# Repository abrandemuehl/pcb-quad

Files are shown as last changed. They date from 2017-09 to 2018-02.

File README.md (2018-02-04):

# UIUC ECE395 PCB Quadcopter Project
The goal of the project was to design a quadcopter with a PCB frame and as many
parts as possible soldered directly onto it. We put an STM32F4, and a BNO055 
IMU onto the board, and purchased external ESC's for the motors.

### Results
Due to difficulties with a parts order through the school, we were not able to 
sufficiently test the hardware before a final version was due. We missed a pull
up resistor on the BNO055's NRESET pin, causing it to constantly be in a state 
of reset, and making it unusable. We fixed it by taping our breakout board IMU 
onto the board, and connecting the necessary wires. After that, we had working 
hardware, but were not able to finish tuning the quadcopter before a failure 
broke one of the motors. We did not have a tuning rig, so we were forced to tune
it by attempting to hover at about floor level. Eventually, one of the motors 
that we used failed, ending the project with working hardware and software, but
incomplete tuning.

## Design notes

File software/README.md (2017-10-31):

# Single Board Quadcopter Software

Uses ST's [CMSIS distribution for the STM32F427xx](http://www.st.com/en/embedded-software/stsw-stm32065.html) for the chip specific information

## Setting up the linux serial port
`stty -F /dev/ttyUSB0 115200 cs8 -cstopb -parenb`

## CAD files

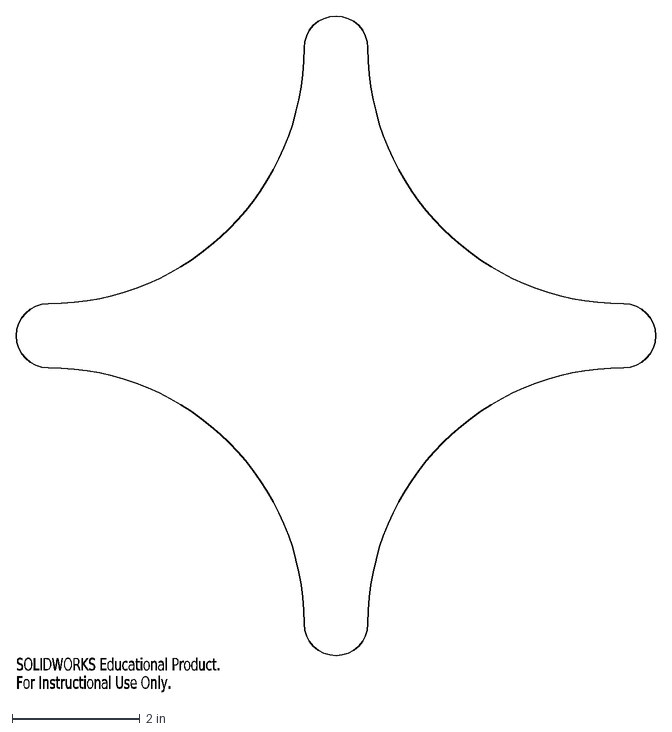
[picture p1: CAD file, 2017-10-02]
hardware/Board_Outline.DXF
SOLIDWORKS Educational Product.
For Instructional Use Only.

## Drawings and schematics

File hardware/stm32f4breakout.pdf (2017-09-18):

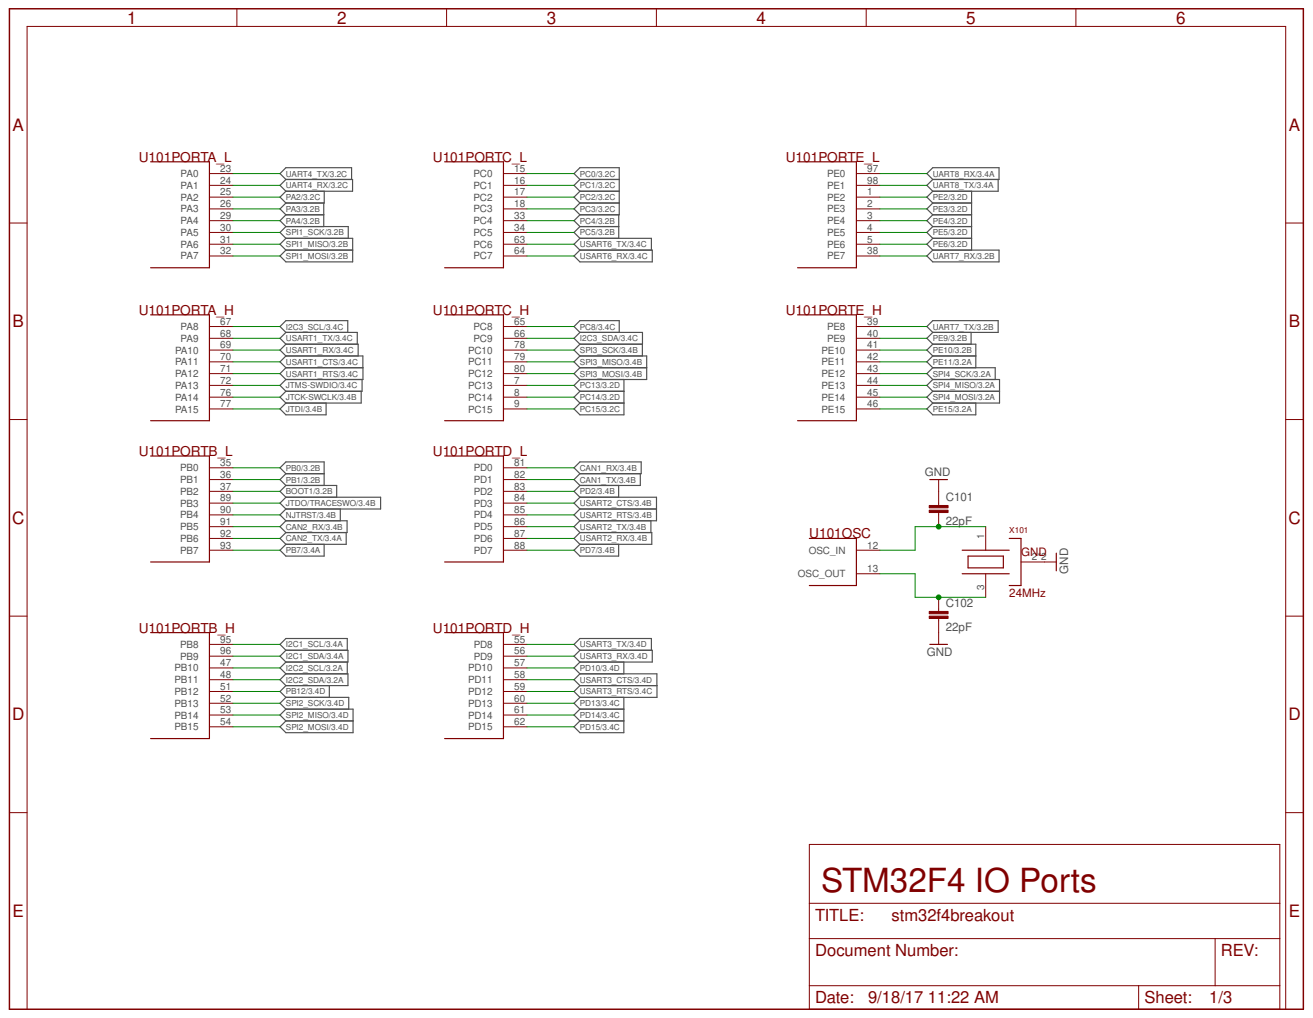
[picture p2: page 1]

Document Number: | REV:

Date: 9/18/17 11:22 AM | Sheet: 1/3

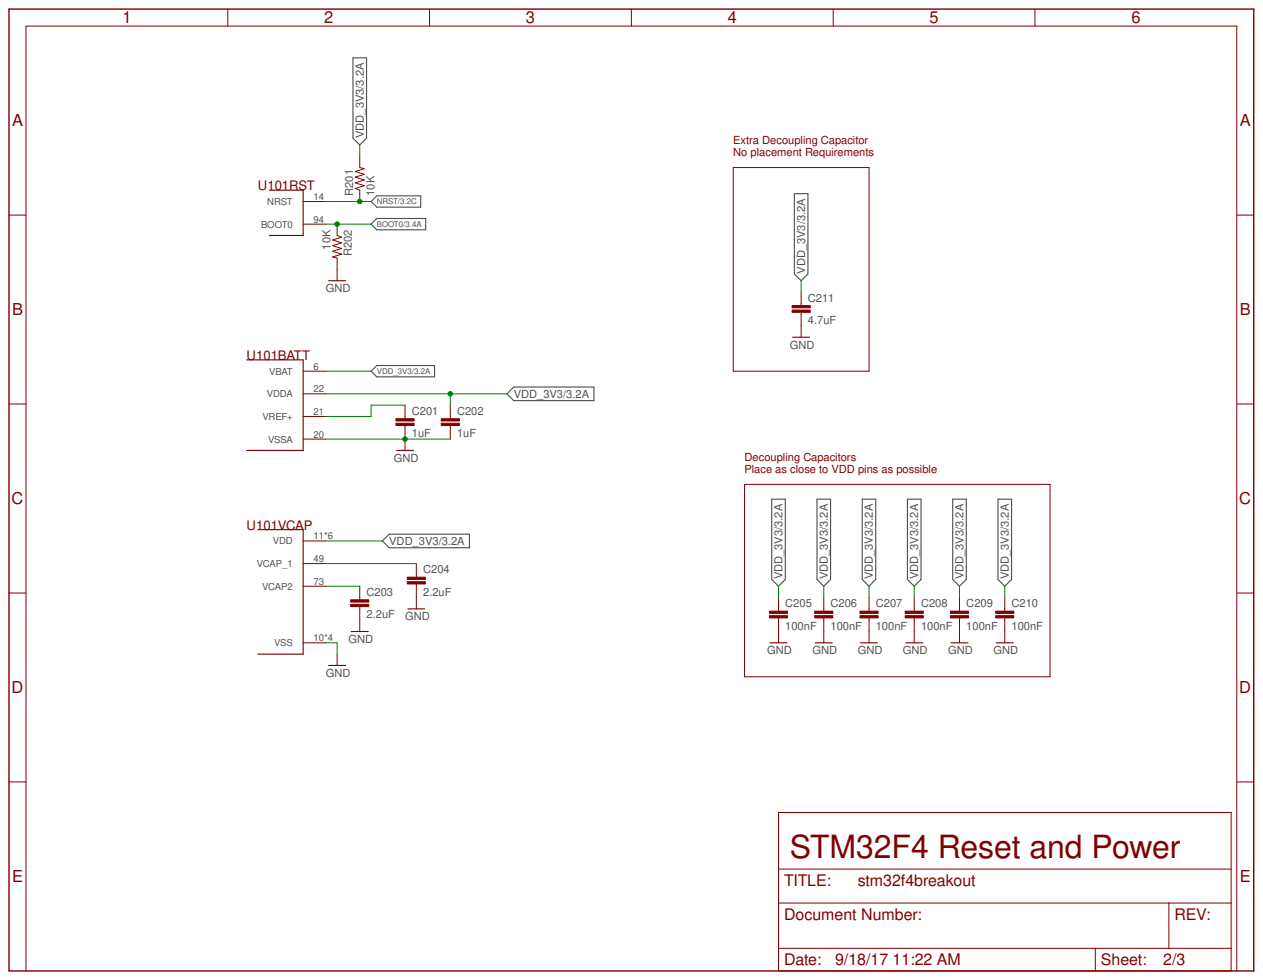
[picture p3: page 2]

Extra Decoupling Capacitor No placement Requirements A

Decoupling Capacitors Place as close to VDD pins as possible

Document Number: | REV:

Date: 9/18/17 11:22 AM | Sheet: 2/3

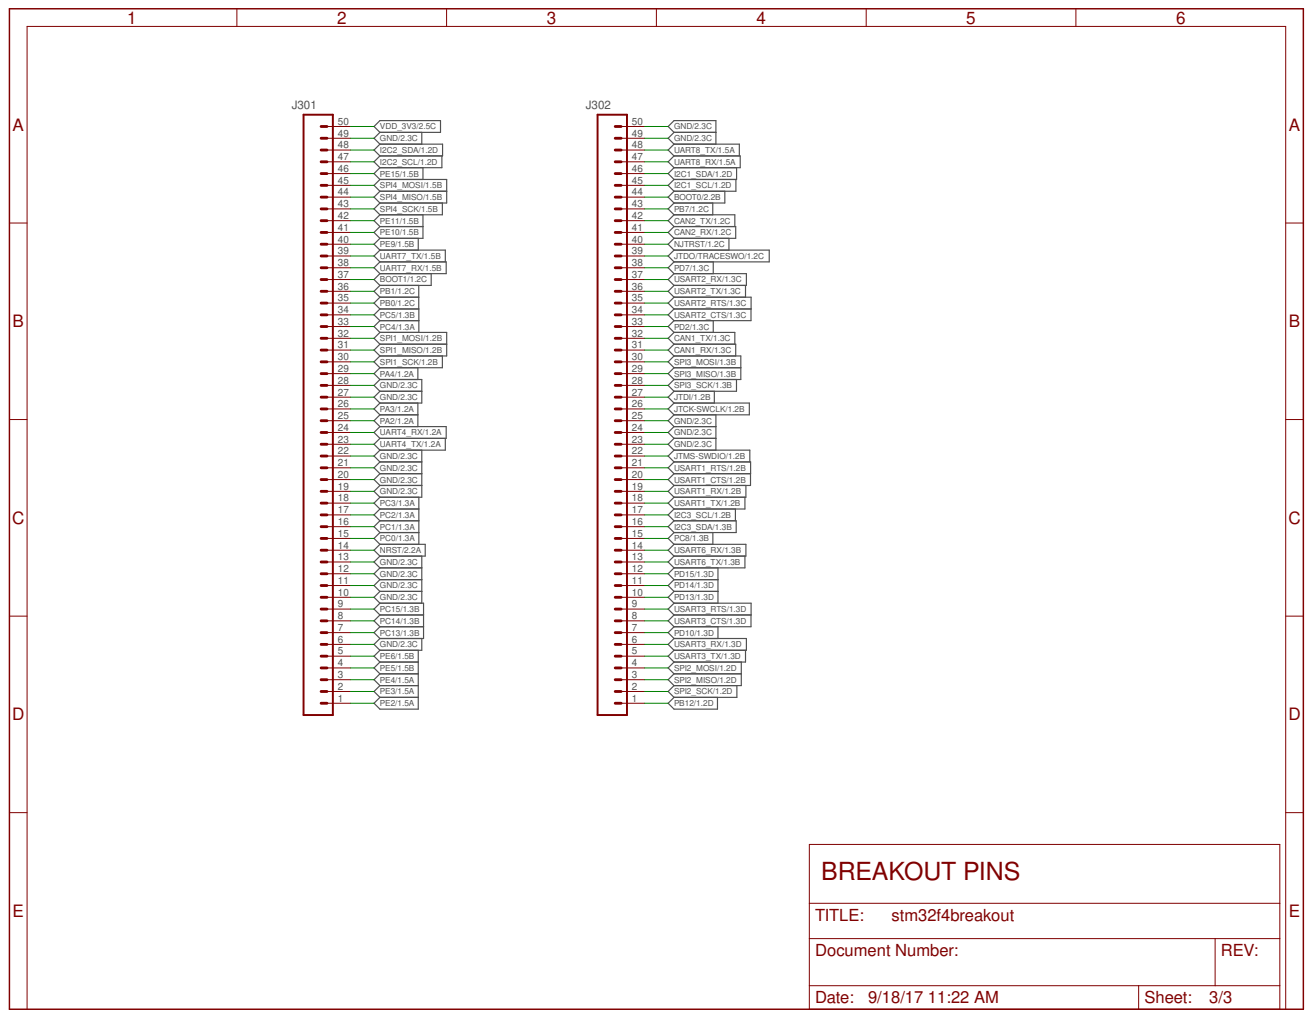
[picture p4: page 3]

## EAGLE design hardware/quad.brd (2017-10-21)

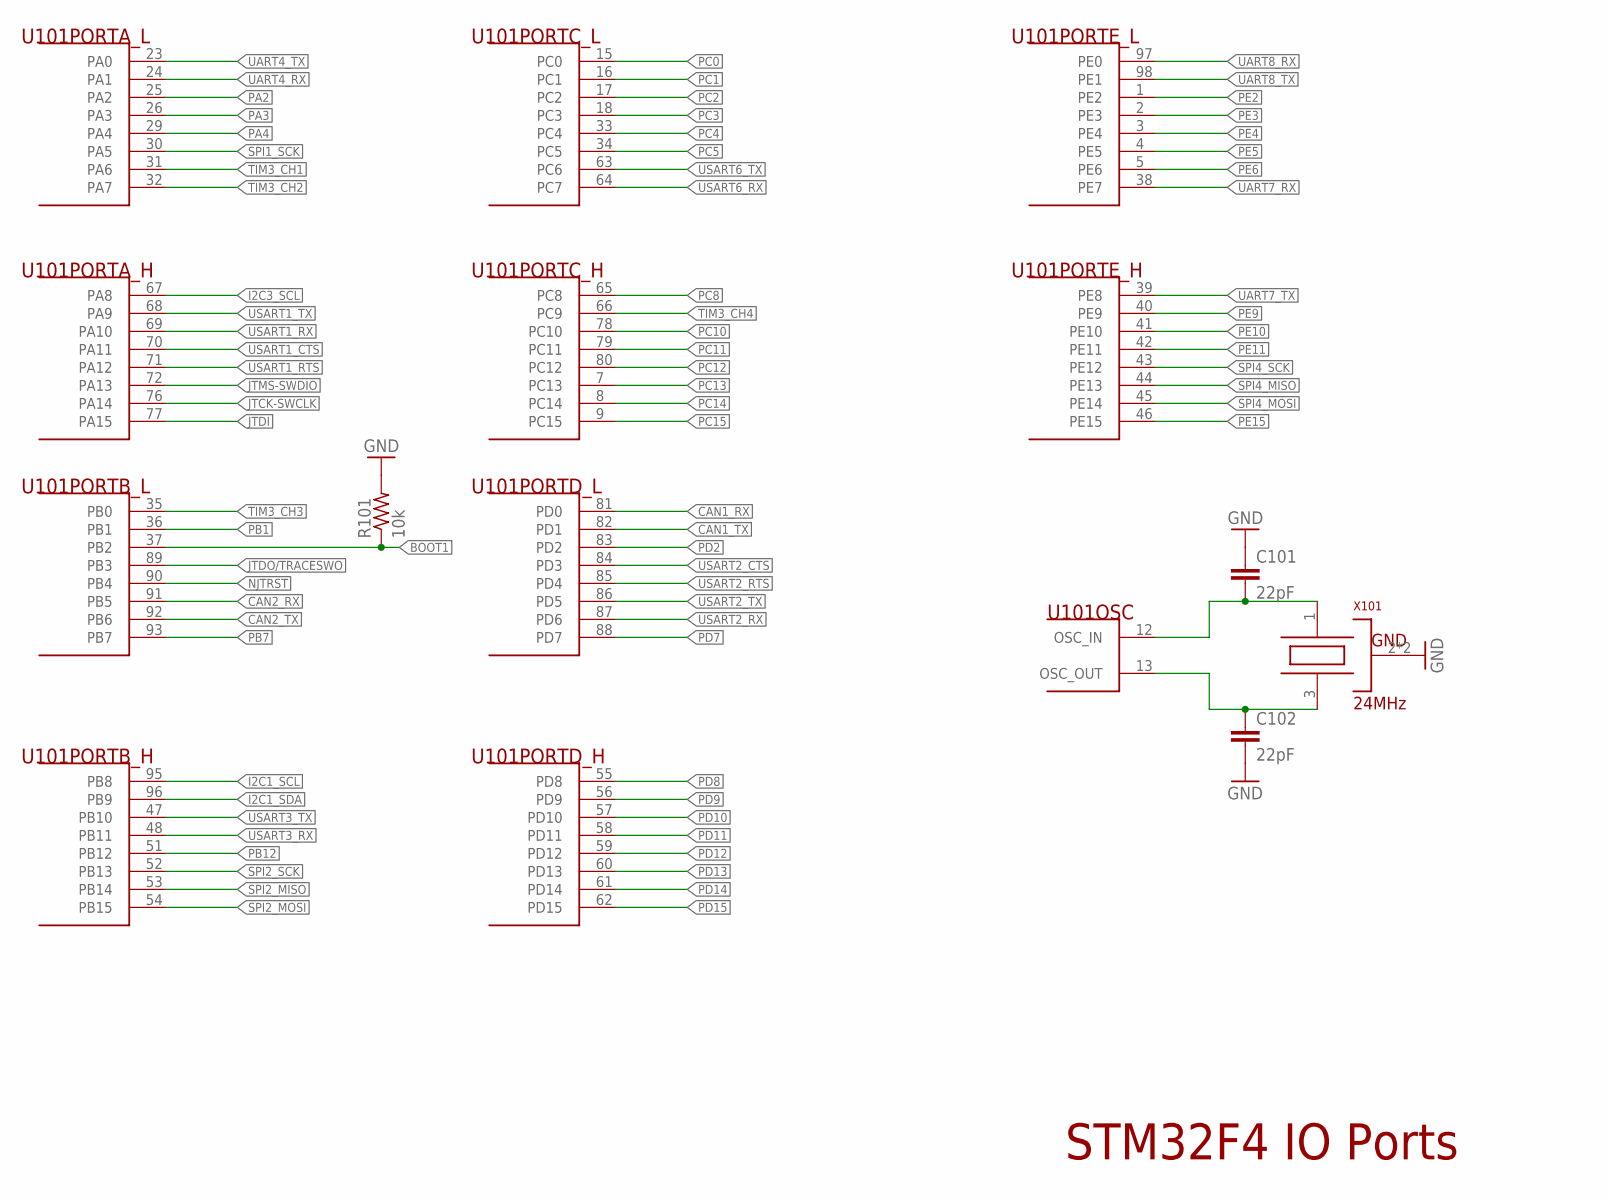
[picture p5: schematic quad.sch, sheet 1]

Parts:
C101, C102: 22pF; C0603
R101: 10k; R0603
U101: STM32F427VGT6; LQFP-100
X101: 24MHz; OSC3.2X2.5

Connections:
BOOT1: R101.1, U101.37 (PB2)
CAN1_RX: U101.81 (PD0)
CAN1_TX: U101.82 (PD1)
CAN2_RX: U101.91 (PB5)
CAN2_TX: U101.92 (PB6)
GND: C101.1, C102.2, R101.2, X101.2 (GND), X101.4 (GND); also elsewhere on the board
I2C1_SCL: U101.95 (PB8); also elsewhere on the board
I2C1_SDA: U101.96 (PB9); also elsewhere on the board
I2C3_SCL: U101.67 (PA8)
JTCK-SWCLK: U101.76 (PA14)
JTDI: U101.77 (PA15)
JTDO/TRACESWO: U101.89 (PB3)
JTMS-SWDIO: U101.72 (PA13)
NJTRST: U101.90 (PB4)
OSC_IN: C101.2, U101.12 (OSC_IN), X101.1 (OSC1)
OSC_OUT: C102.1, U101.13 (OSC_OUT), X101.3 (OSC2)
PA2: U101.25 (PA2)
PA3: U101.26 (PA3)
PA4: U101.29 (PA4)
PB1: U101.36 (PB1)
PB7: U101.93 (PB7)
PB12: U101.51 (PB12)
PC0: U101.15 (PC0)
PC1: U101.16 (PC1)
PC2: U101.17 (PC2)
PC3: U101.18 (PC3)
PC4: U101.33 (PC4)
PC5: U101.34 (PC5)
PC8: U101.65 (PC8)
PC10: U101.78 (PC10)
PC11: U101.79 (PC11)
PC12: U101.80 (PC12)
PC13: U101.7 (PC13)
PC14: U101.8 (PC14)
PC15: U101.9 (PC15)
PD2: U101.83 (PD2); also elsewhere on the board
PD7: U101.88 (PD7)
PD8: U101.55 (PD8)
PD9: U101.56 (PD9)
PD10: U101.57 (PD10)
PD11: U101.58 (PD11)
PD12: U101.59 (PD12)
PD13: U101.60 (PD13)
PD14: U101.61 (PD14)
PD15: U101.62 (PD15)
PE2: U101.1 (PE2)
PE3: U101.2 (PE3)
PE4: U101.3 (PE4)
PE5: U101.4 (PE5)
PE6: U101.5 (PE6)
PE9: U101.40 (PE9)
PE10: U101.41 (PE10)
PE11: U101.42 (PE11)
PE15: U101.46 (PE15)
SPI1_SCK: U101.30 (PA5)
SPI2_MISO: U101.53 (PB14)
SPI2_MOSI: U101.54 (PB15)
SPI2_SCK: U101.52 (PB13)
SPI4_MISO: U101.44 (PE13)
SPI4_MOSI: U101.45 (PE14)
SPI4_SCK: U101.43 (PE12)
TIM3_CH1: U101.31 (PA6); also elsewhere on the board
TIM3_CH2: U101.32 (PA7); also elsewhere on the board
TIM3_CH3: U101.35 (PB0); also elsewhere on the board
TIM3_CH4: U101.66 (PC9); also elsewhere on the board
UART4_RX: U101.24 (PA1)
UART4_TX: U101.23 (PA0)
UART7_RX: U101.38 (PE7)
UART7_TX: U101.39 (PE8)
UART8_RX: U101.97 (PE0)
UART8_TX: U101.98 (PE1)
USART1_CTS: U101.70 (PA11)
USART1_RTS: U101.71 (PA12)
USART1_RX: U101.69 (PA10); also elsewhere on the board
USART1_TX: U101.68 (PA9); also elsewhere on the board
USART2_CTS: U101.84 (PD3)
USART2_RTS: U101.85 (PD4)
USART2_RX: U101.87 (PD6)
USART2_TX: U101.86 (PD5)
USART3_RX: U101.48 (PB11); also elsewhere on the board
USART3_TX: U101.47 (PB10); also elsewhere on the board
USART6_RX: U101.64 (PC7)
USART6_TX: U101.63 (PC6)

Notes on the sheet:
STM32F4 IO Ports

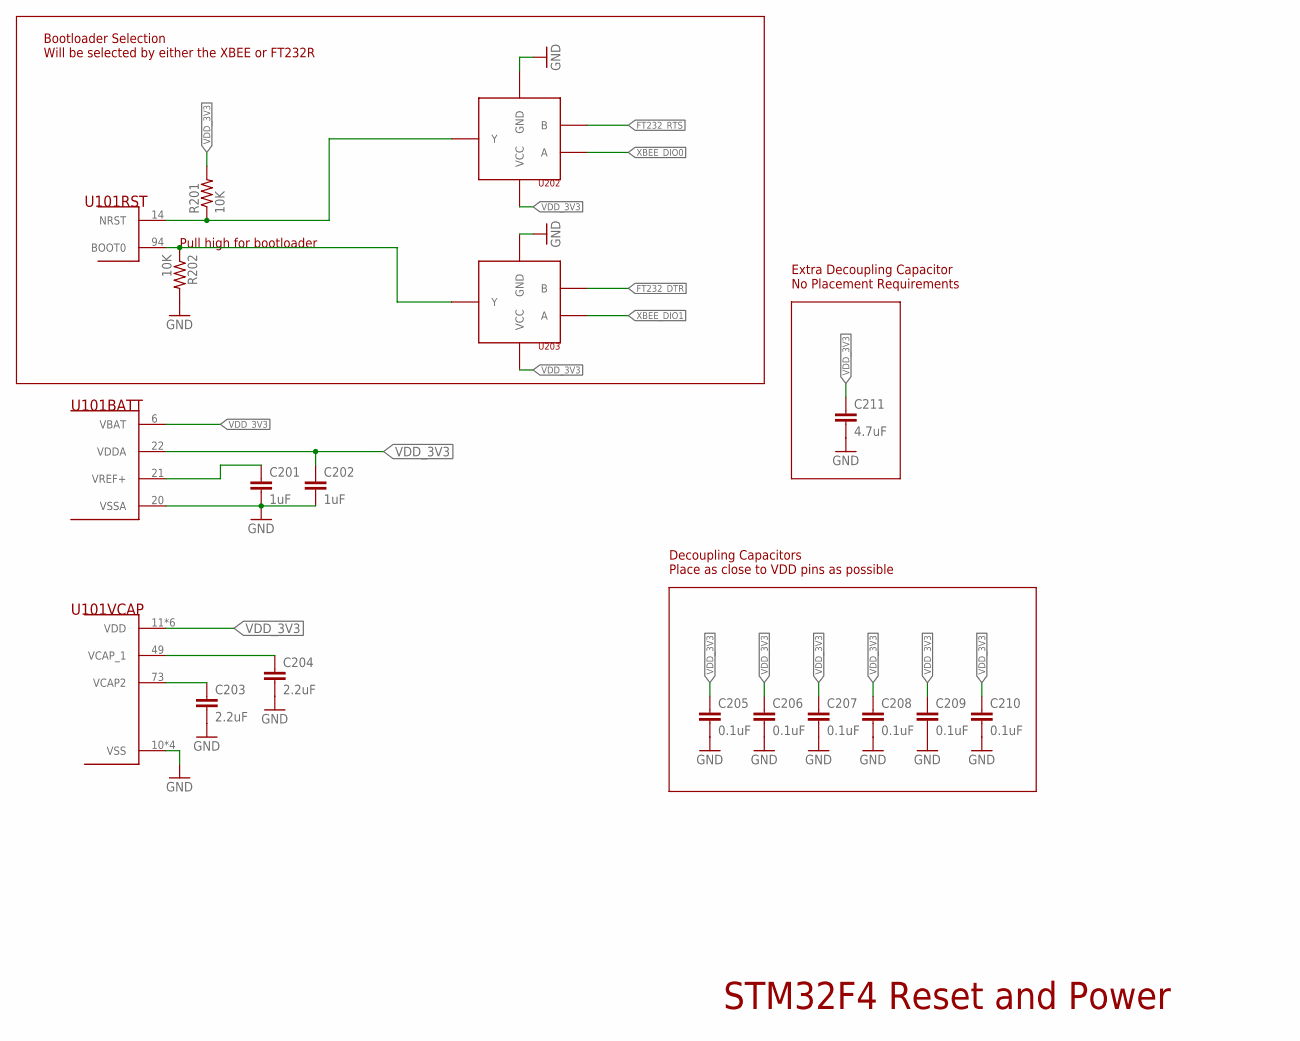
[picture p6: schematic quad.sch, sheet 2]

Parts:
C201, C202: 1uF; C0603
C203, C204: 2.2uF; C0603
C205, C206, C207, C208, C209, C210: 0.1uF; C0603
C211: 4.7uF; C0603
R201, R202: 10K; R0603
U101: STM32F427VGT6; LQFP-100
U202: AND_GATE; SOT23-5L
U203: SN74AHC1G32DBVR; SOT23-5L

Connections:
BOOT0: R202.1, U101.94 (BOOT0), U203.4 (Y)
FT232_DTR: U203.2 (B); also elsewhere on the board
FT232_RTS: U202.2 (B); also elsewhere on the board
GND: C201.2, C202.2, C203.2, C204.2, C205.2, C206.2, C207.2, C208.2, C209.2, C210.2, C211.2, R202.2, U101.10 (VSS), U101.20 (VSSA), U101.27 (VSS), U101.74 (VSS), U101.99 (VSS), U202.3 (GND), U203.3 (GND); also elsewhere on the board
NRST: R201.1, U101.14 (NRST), U202.4 (Y)
VCAP2: C203.1, U101.73 (VCAP2)
VCAP_1: C204.1, U101.49 (VCAP_1)
VDD_3V3: C201.1, C202.1, C205.1, C206.1, C207.1, C208.1, C209.1, C210.1, C211.1, R201.2, U101.6 (VBAT), U101.11 (VDD), U101.19 (VDD), U101.21 (VREF+), U101.22 (VDDA), U101.28 (VDD), U101.50 (VDD), U101.75 (VDD), U101.100 (VDD), U202.5 (VCC), U203.5 (VCC); also elsewhere on the board
XBEE_DIO0: U202.1 (A); also elsewhere on the board
XBEE_DIO1: U203.1 (A); also elsewhere on the board

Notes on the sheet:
STM32F4 Reset and Power
Decoupling Capacitors Place as close to VDD pins as possible
Extra Decoupling Capacitor No Placement Requirements
Pull high for bootloader
Bootloader Selection Will be selected by either the XBEE or FT232R

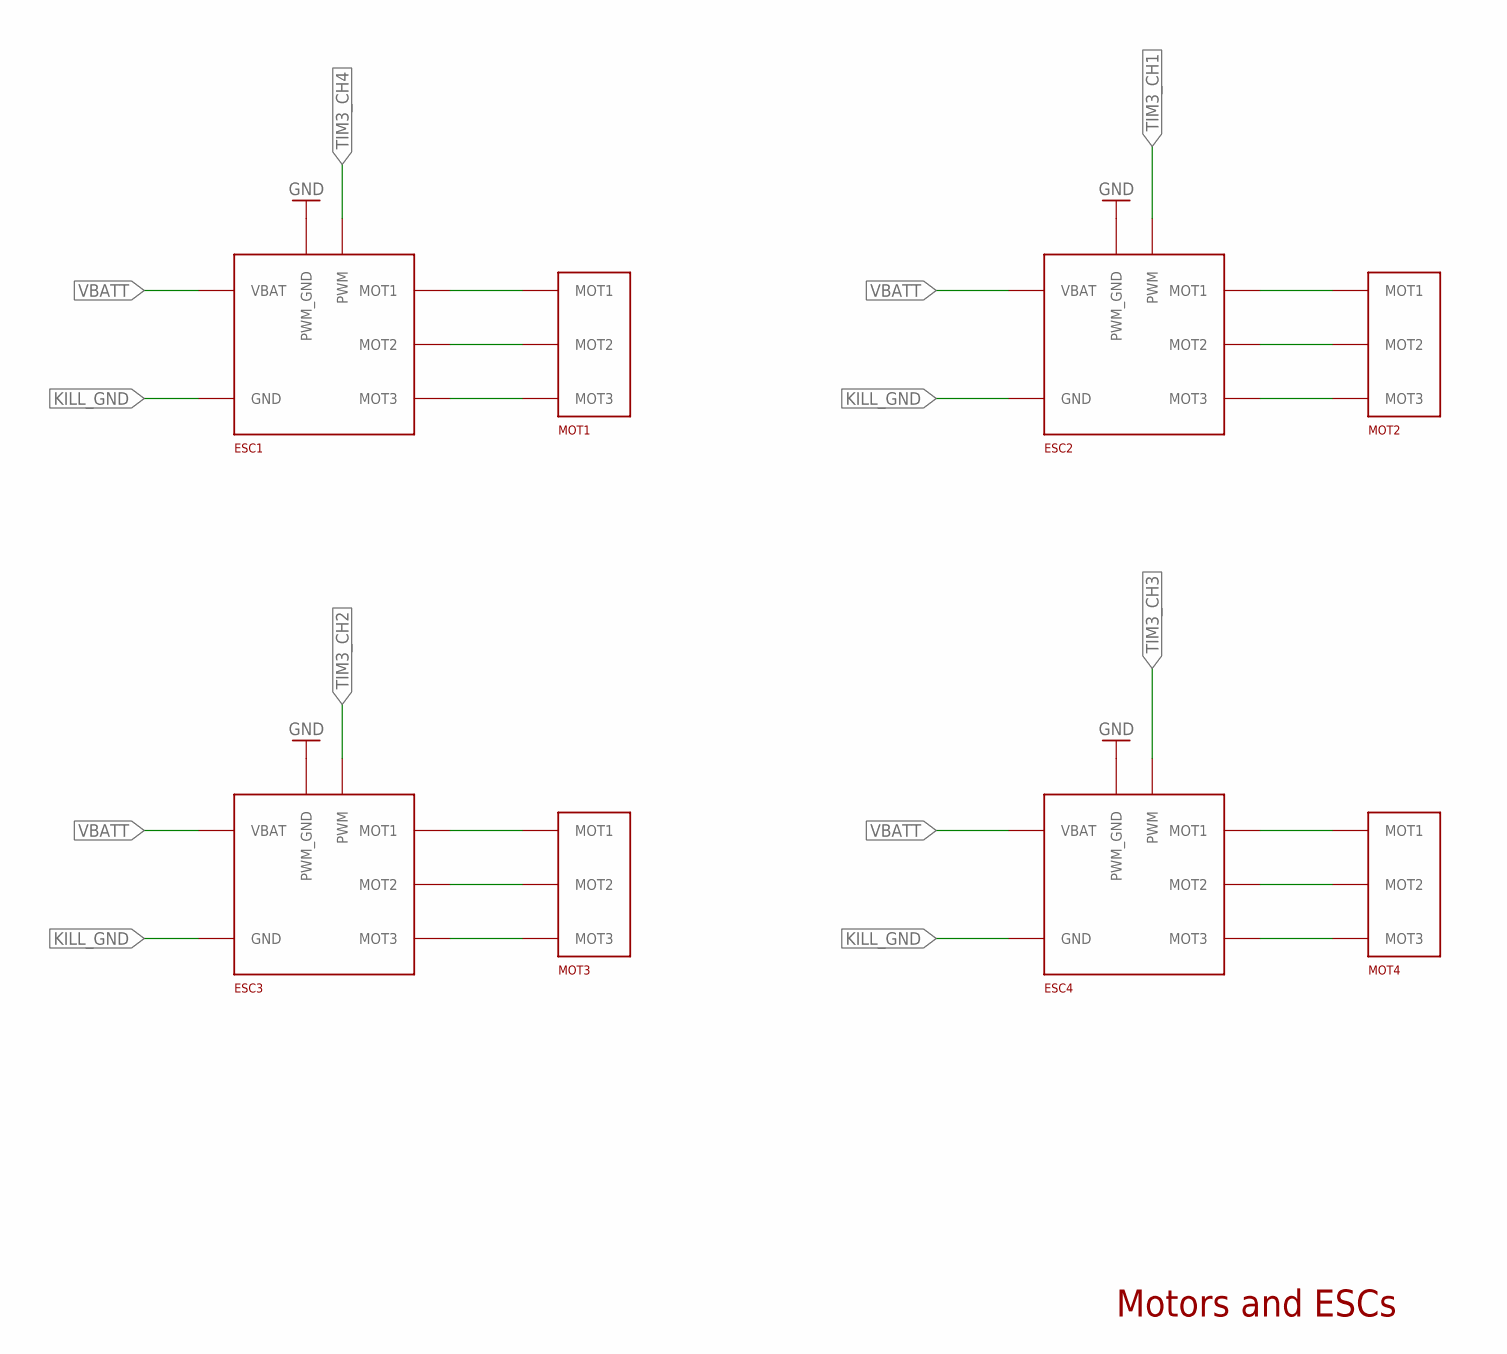
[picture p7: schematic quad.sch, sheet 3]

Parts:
ESC1, ESC2, ESC3, ESC4: AFRO_ESC
MOT1, MOT2, MOT3, MOT4: MOTOR

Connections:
GND: ESC1.PWM_GND, ESC2.PWM_GND, ESC3.PWM_GND, ESC4.PWM_GND; also elsewhere on the board
KILL_GND: ESC1.GND, ESC2.GND, ESC3.GND, ESC4.GND; also elsewhere on the board
MOT1_1: ESC1.MOT1, MOT1.MOT1
MOT1_2: ESC1.MOT2, MOT1.MOT2
MOT1_3: ESC1.MOT3, MOT1.MOT3
MOT2_1: ESC2.MOT1, MOT2.MOT1
MOT_2_2: ESC2.MOT2, MOT2.MOT2
MOT_2_3: ESC2.MOT3, MOT2.MOT3
MOT_3_1: ESC3.MOT1, MOT3.MOT1
MOT_3_2: ESC3.MOT2, MOT3.MOT2
MOT_3_3: ESC3.MOT3, MOT3.MOT3
MOT_4_1: ESC4.MOT1, MOT4.MOT1
MOT_4_2: ESC4.MOT2, MOT4.MOT2
MOT_4_3: ESC4.MOT3, MOT4.MOT3
TIM3_CH1: ESC2.PWM; also elsewhere on the board
TIM3_CH2: ESC3.PWM; also elsewhere on the board
TIM3_CH3: ESC4.PWM; also elsewhere on the board
TIM3_CH4: ESC1.PWM; also elsewhere on the board
VBATT: ESC1.VBATT (VBAT), ESC2.VBATT (VBAT), ESC3.VBATT (VBAT), ESC4.VBATT (VBAT); also elsewhere on the board

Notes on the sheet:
Motors and ESCs

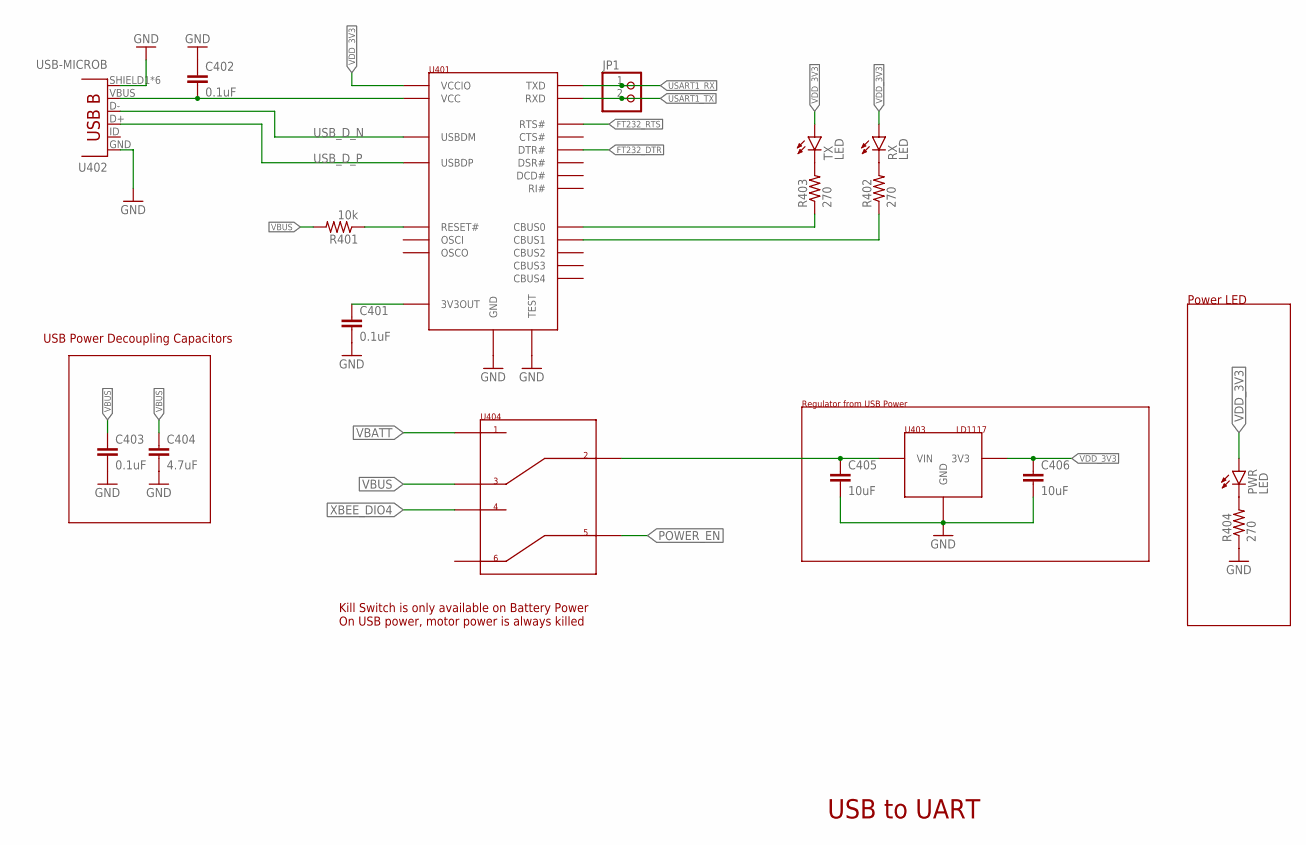
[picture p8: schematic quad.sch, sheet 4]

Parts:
C401, C402, C403: 0.1uF; C0603
C404: 4.7uF; C0603
C405, C406: 10uF; C0603
JP1: PINHD-1X2; 1X02
PWR: LED; LED-0603
R401: 10k; R0603
R402, R403, R404: 270; R0603
RX: LED; LED-0603
TX: LED; LED-0603
U401: FT232R; SSOP28
U402: USB-MICROB; USB-B-MICRO-SMD
U403: LD1117; SOT223
U404: MFS201N-16-Z

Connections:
FT232_DTR: U401.2 (DTR#); also elsewhere on the board
FT232_RTS: U401.3 (RTS#); also elsewhere on the board
GND: C401.2, C402.1, C403.2, C404.2, C405.2, C406.2, R404.1, U401.7 (GND), U401.18 (GND), U401.21 (GND), U401.25 (GND), U401.26 (TEST), U402.GND, U402.SHIELD1 (SHIELD), U402.SHIELD2 (SHIELD), U402.SHIELD3 (SHIELD), U402.SHIELD4 (SHIELD), U402.SHIELD5 (SHIELD), U402.SHIELD6 (SHIELD), U403.1 (GND); also elsewhere on the board
unnamed: R401.1, U401.19 (RESET#)
unnamed: C401.1, U401.17 (3V3OUT)
unnamed: R403.1, U401.23 (CBUS0)
unnamed: R402.1, U401.22 (CBUS1)
unnamed: R402.2, RX.C
unnamed: R403.2, TX.C
unnamed: PWR.C, R404.2
POWER_EN: U404.5; also elsewhere on the board
PWR: C405.1, U403.3 (VIN), U404.2
USART1_RX: JP1.1, U401.1 (TXD); also elsewhere on the board
USART1_TX: JP1.2, U401.5 (RXD); also elsewhere on the board
USB_D_N: U401.16 (USBDM), U402.D-
USB_D_P: U401.15 (USBDP), U402.D+
VBATT: U404.1; also elsewhere on the board
VBUS: C402.2, C403.1, C404.1, R401.2, U401.20 (VCC), U402.VBUS, U404.3
VDD_3V3: C406.1, PWR.A, RX.A, TX.A, U401.4 (VCCIO), U403.2 (3V3), U403.4 (3V3); also elsewhere on the board
XBEE_DIO4: U404.4; also elsewhere on the board

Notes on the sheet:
USB to UART
USB Power Decoupling Capacitors
Regulator from USB Power
Kill Switch is only available on Battery Power On USB power, motor power is always killed
Power LED

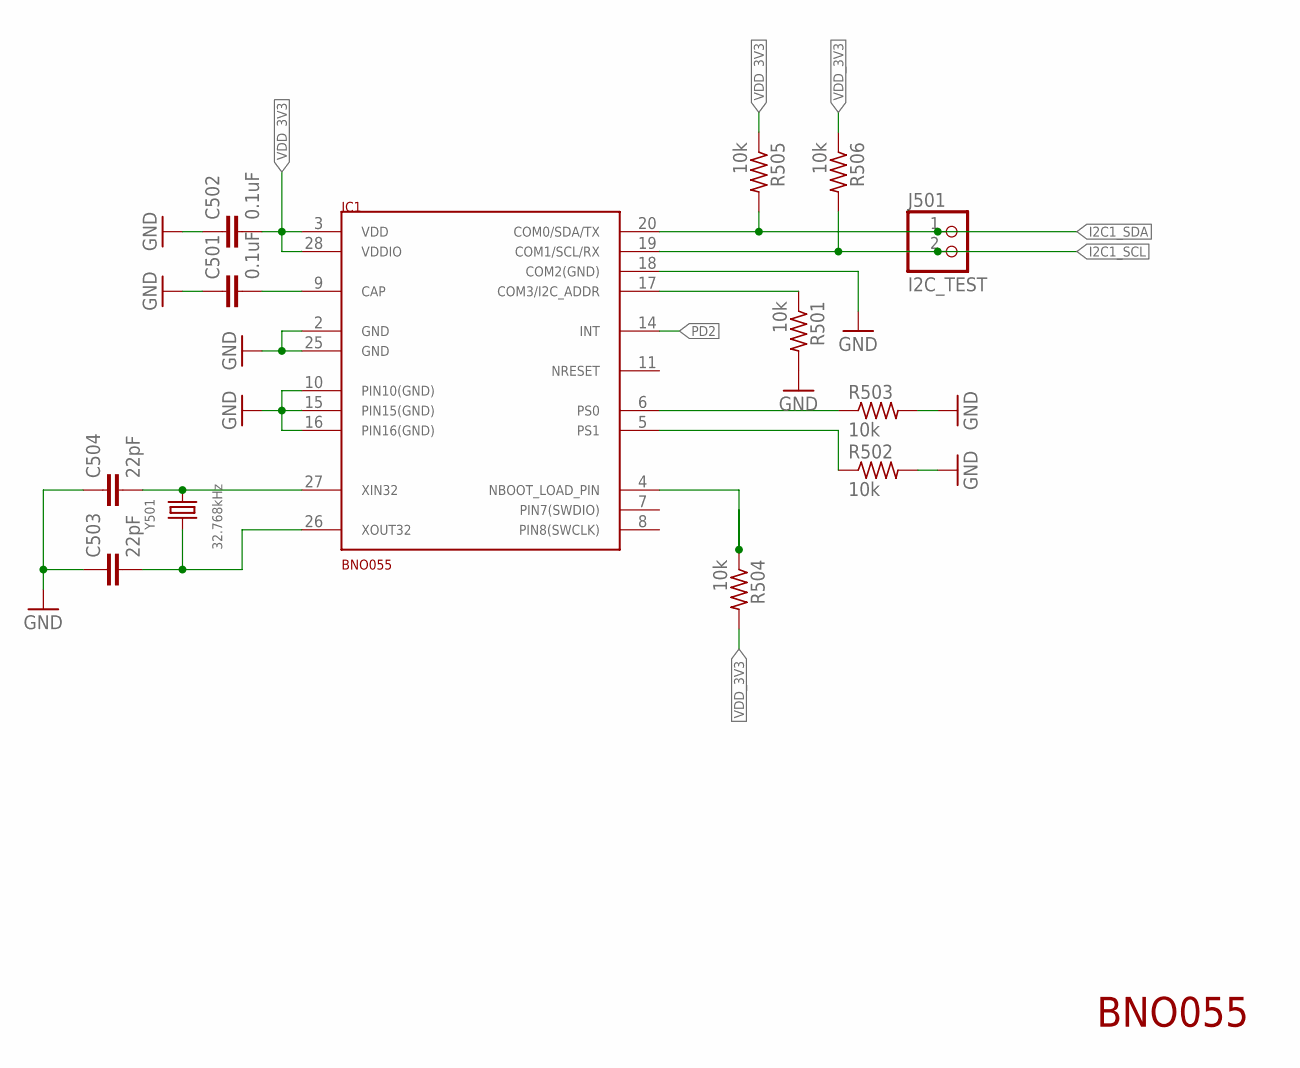
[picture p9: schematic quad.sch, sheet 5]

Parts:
C501, C502: 0.1uF; C0603
C503, C504: 22pF; C0603
IC1: BNO055; LGA-28_3.80X5.20/0.5
J501: I2C_TEST; 1X02
R501, R502, R503, R504, R505, R506: 10k; R0603
Y501: 32.768kHz; ABS25

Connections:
GND: C501.1, C502.1, C503.1, C504.1, IC1.2, IC1.10, IC1.15, IC1.16, IC1.18, IC1.25, R501.2, R502.2, R503.2; also elsewhere on the board
I2C1_SCL: IC1.19, J501.2, R506.2; also elsewhere on the board
I2C1_SDA: IC1.20, J501.1, R505.2; also elsewhere on the board
unnamed: C501.2, IC1.9
unnamed: C504.2, IC1.27, Y501.4 (2)
unnamed: C503.2, IC1.26, Y501.1
unnamed: IC1.17, R501.1
unnamed: IC1.6, R503.1
unnamed: IC1.5, R502.1
unnamed: IC1.4, R504.1
PD2: IC1.14; also elsewhere on the board
VDD_3V3: C502.2, IC1.3, IC1.28, R504.2, R505.1, R506.1; also elsewhere on the board

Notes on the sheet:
BNO055

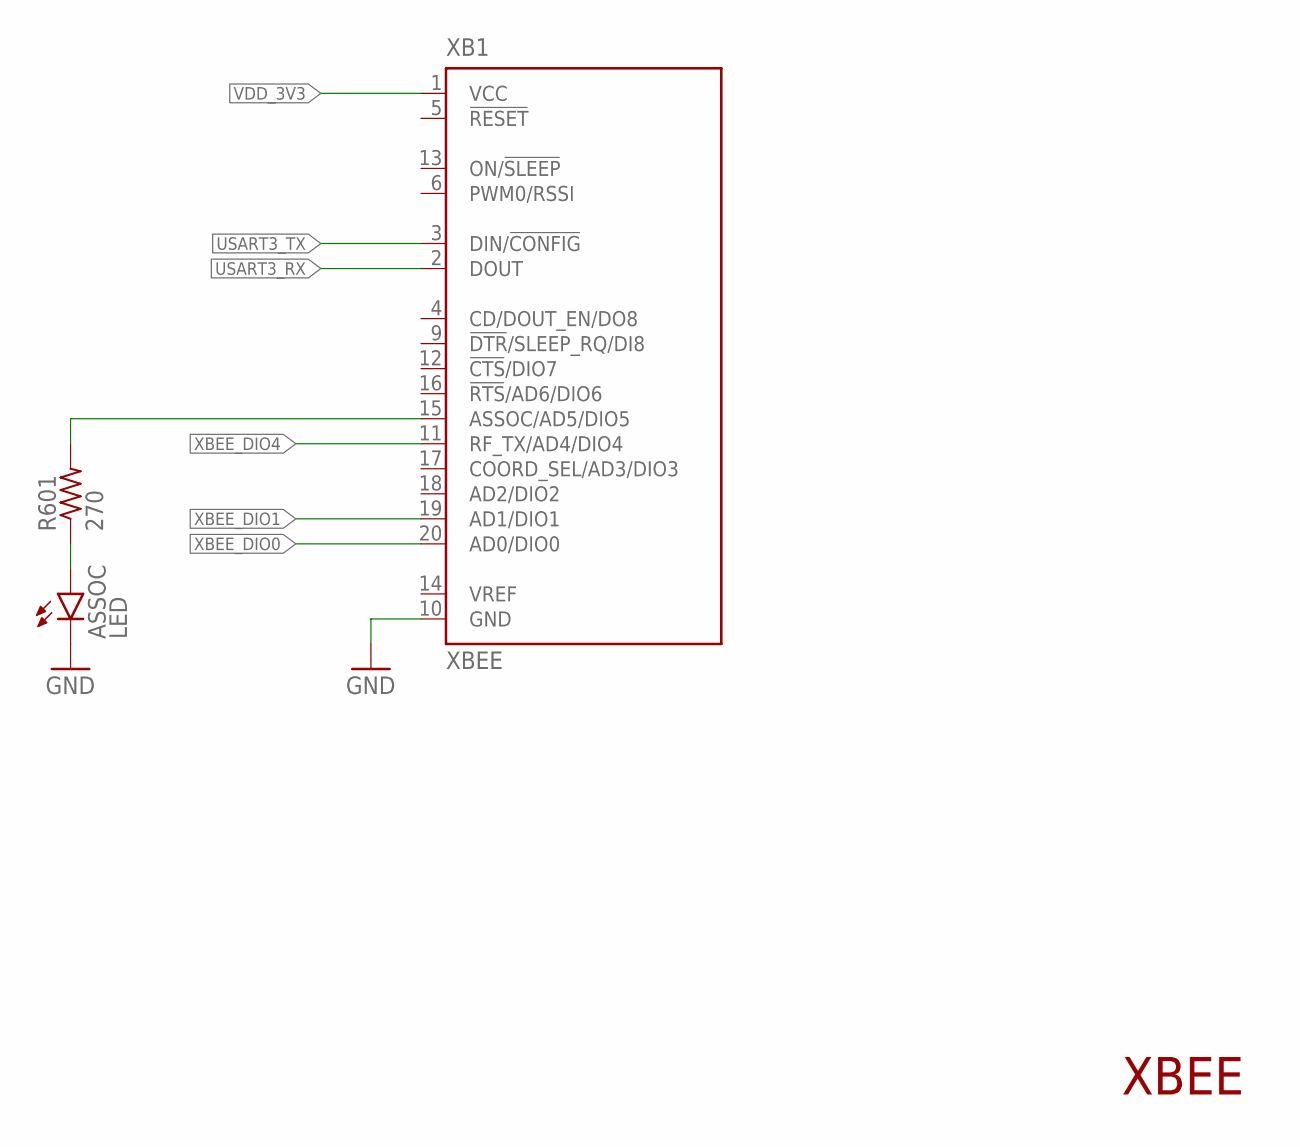
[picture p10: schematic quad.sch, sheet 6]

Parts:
ASSOC: LED; LED-0603
R601: 270; R0603
XB1: XBEE

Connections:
GND: ASSOC.C, XB1.10 (GND); also elsewhere on the board
unnamed: ASSOC.A, R601.1
unnamed: R601.2, XB1.15 (ASSOC/AD5/DIO5)
USART3_RX: XB1.2 (DOUT); also elsewhere on the board
USART3_TX: XB1.3 (DIN/!CONFIG); also elsewhere on the board
VDD_3V3: XB1.1 (VCC); also elsewhere on the board
XBEE_DIO0: XB1.20 (AD0/DIO0); also elsewhere on the board
XBEE_DIO1: XB1.19 (AD1/DIO1); also elsewhere on the board
XBEE_DIO4: XB1.11 (RF_TX/AD4/DIO4); also elsewhere on the board

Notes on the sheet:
XBEE

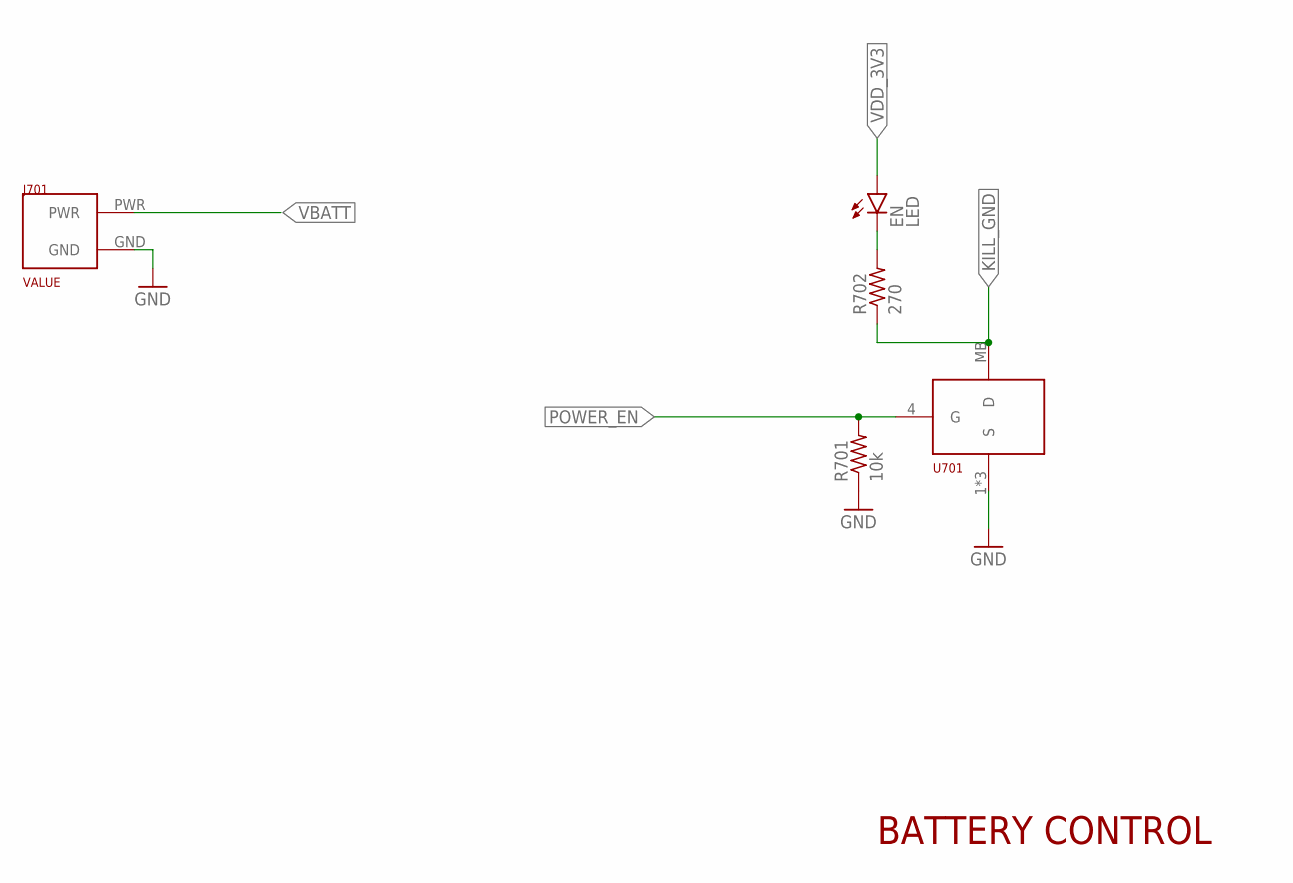
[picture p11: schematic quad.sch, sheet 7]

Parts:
EN: LED; LED-0603
J701: XT60
R701: 10k; R0603
R702: 270; R0603
U701: PSMN9RS-30YLC; SOT669

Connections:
GND: J701.GND, R701.1, U701.1 (S), U701.2 (S), U701.3 (S); also elsewhere on the board
KILL_GND: R702.1, U701.MB (D); also elsewhere on the board
unnamed: EN.C, R702.2
POWER_EN: R701.2, U701.4 (G); also elsewhere on the board
VBATT: J701.PWR; also elsewhere on the board
VDD_3V3: EN.A; also elsewhere on the board

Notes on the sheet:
BATTERY CONTROL

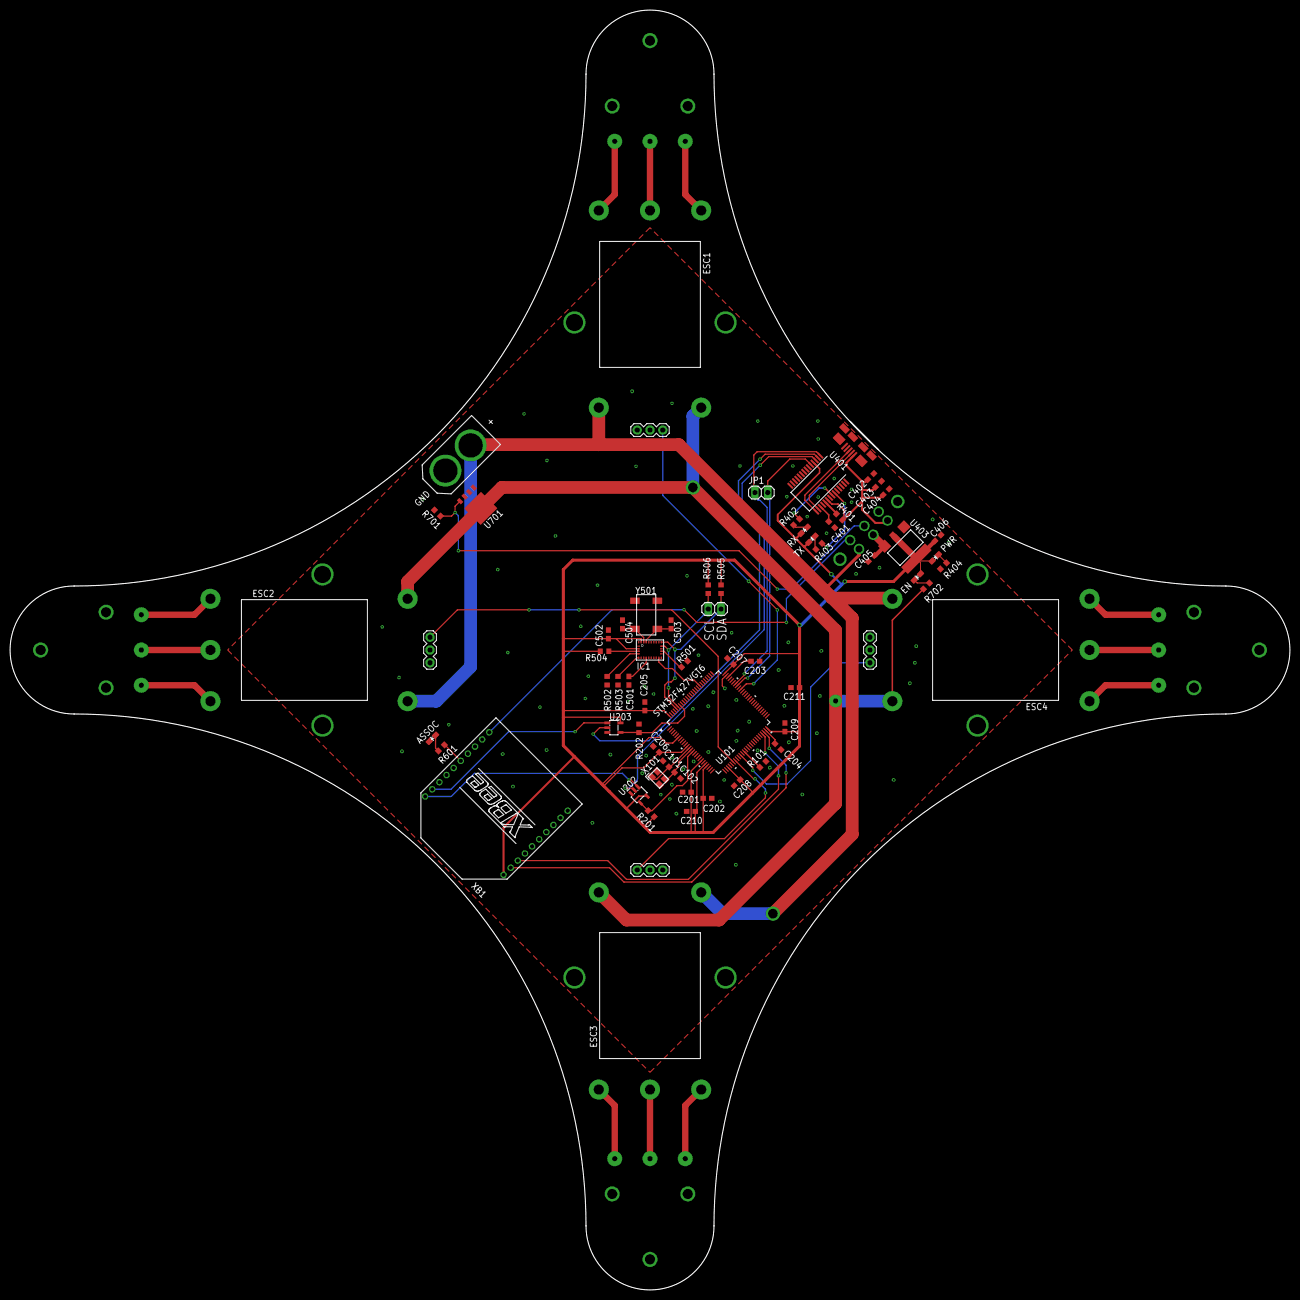
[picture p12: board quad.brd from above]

Board: 2 copper layers, 254.0 x 254.0 mm, 67 parts (0 on the bottom side), 61 nets.

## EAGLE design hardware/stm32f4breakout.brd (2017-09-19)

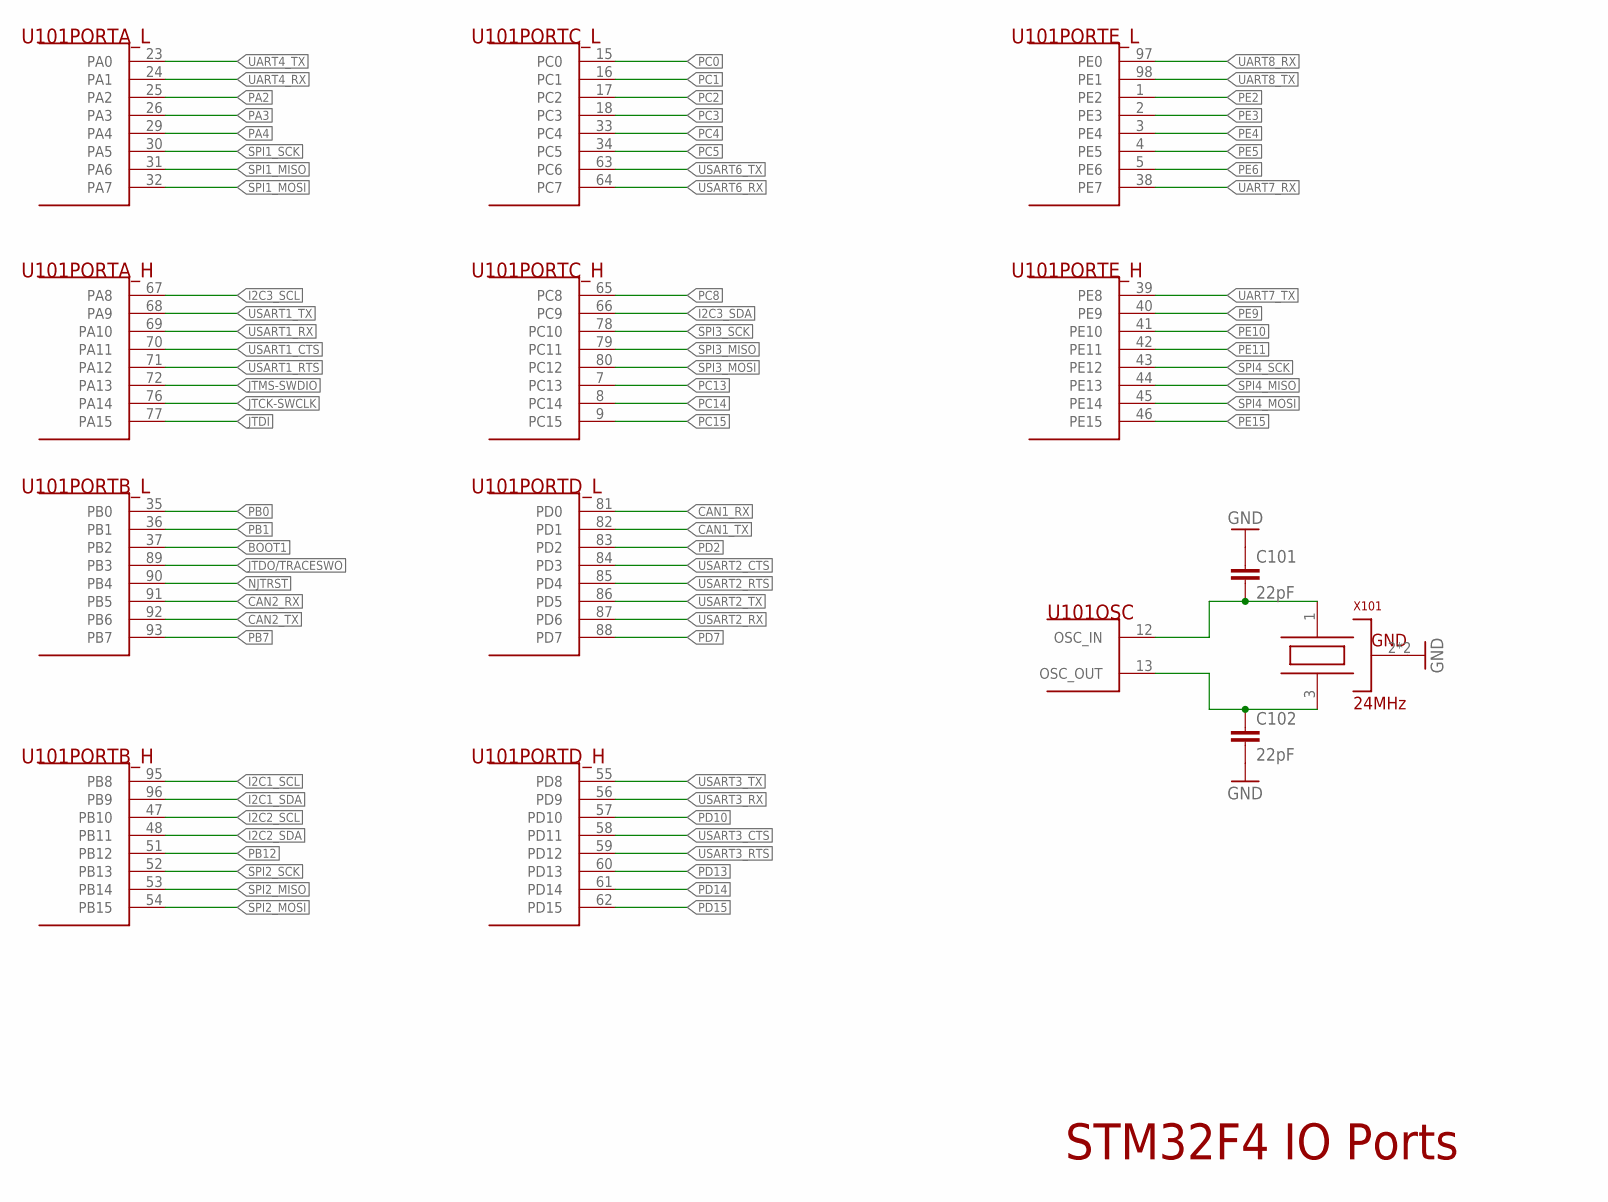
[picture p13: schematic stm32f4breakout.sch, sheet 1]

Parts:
C101, C102: 22pF; C0603
U101: STM32F427VGT6; LQFP-100
X101: 24MHz; OSC3.2X2.5

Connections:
BOOT1: U101.37 (PB2); also elsewhere on the board
CAN1_RX: U101.81 (PD0); also elsewhere on the board
CAN1_TX: U101.82 (PD1); also elsewhere on the board
CAN2_RX: U101.91 (PB5); also elsewhere on the board
CAN2_TX: U101.92 (PB6); also elsewhere on the board
GND: C101.1, C102.2, X101.2 (GND), X101.4 (GND); also elsewhere on the board
I2C1_SCL: U101.95 (PB8); also elsewhere on the board
I2C1_SDA: U101.96 (PB9); also elsewhere on the board
I2C2_SCL: U101.47 (PB10); also elsewhere on the board
I2C2_SDA: U101.48 (PB11); also elsewhere on the board
I2C3_SCL: U101.67 (PA8); also elsewhere on the board
I2C3_SDA: U101.66 (PC9); also elsewhere on the board
JTCK-SWCLK: U101.76 (PA14); also elsewhere on the board
JTDI: U101.77 (PA15); also elsewhere on the board
JTDO/TRACESWO: U101.89 (PB3); also elsewhere on the board
JTMS-SWDIO: U101.72 (PA13); also elsewhere on the board
NJTRST: U101.90 (PB4); also elsewhere on the board
OSC_IN: C101.2, U101.12 (OSC_IN), X101.1 (OSC1)
OSC_OUT: C102.1, U101.13 (OSC_OUT), X101.3 (OSC2)
PA2: U101.25 (PA2); also elsewhere on the board
PA3: U101.26 (PA3); also elsewhere on the board
PA4: U101.29 (PA4); also elsewhere on the board
PB0: U101.35 (PB0); also elsewhere on the board
PB1: U101.36 (PB1); also elsewhere on the board
PB7: U101.93 (PB7); also elsewhere on the board
PB12: U101.51 (PB12); also elsewhere on the board
PC0: U101.15 (PC0); also elsewhere on the board
PC1: U101.16 (PC1); also elsewhere on the board
PC2: U101.17 (PC2); also elsewhere on the board
PC3: U101.18 (PC3); also elsewhere on the board
PC4: U101.33 (PC4); also elsewhere on the board
PC5: U101.34 (PC5); also elsewhere on the board
PC8: U101.65 (PC8); also elsewhere on the board
PC13: U101.7 (PC13); also elsewhere on the board
PC14: U101.8 (PC14); also elsewhere on the board
PC15: U101.9 (PC15); also elsewhere on the board
PD2: U101.83 (PD2); also elsewhere on the board
PD7: U101.88 (PD7); also elsewhere on the board
PD10: U101.57 (PD10); also elsewhere on the board
PD13: U101.60 (PD13); also elsewhere on the board
PD14: U101.61 (PD14); also elsewhere on the board
PD15: U101.62 (PD15); also elsewhere on the board
PE2: U101.1 (PE2); also elsewhere on the board
PE3: U101.2 (PE3); also elsewhere on the board
PE4: U101.3 (PE4); also elsewhere on the board
PE5: U101.4 (PE5); also elsewhere on the board
PE6: U101.5 (PE6); also elsewhere on the board
PE9: U101.40 (PE9); also elsewhere on the board
PE10: U101.41 (PE10); also elsewhere on the board
PE11: U101.42 (PE11); also elsewhere on the board
PE15: U101.46 (PE15); also elsewhere on the board
SPI1_MISO: U101.31 (PA6); also elsewhere on the board
SPI1_MOSI: U101.32 (PA7); also elsewhere on the board
SPI1_SCK: U101.30 (PA5); also elsewhere on the board
SPI2_MISO: U101.53 (PB14); also elsewhere on the board
SPI2_MOSI: U101.54 (PB15); also elsewhere on the board
SPI2_SCK: U101.52 (PB13); also elsewhere on the board
SPI3_MISO: U101.79 (PC11); also elsewhere on the board
SPI3_MOSI: U101.80 (PC12); also elsewhere on the board
SPI3_SCK: U101.78 (PC10); also elsewhere on the board
SPI4_MISO: U101.44 (PE13); also elsewhere on the board
SPI4_MOSI: U101.45 (PE14); also elsewhere on the board
SPI4_SCK: U101.43 (PE12); also elsewhere on the board
UART4_RX: U101.24 (PA1); also elsewhere on the board
UART4_TX: U101.23 (PA0); also elsewhere on the board
UART7_RX: U101.38 (PE7); also elsewhere on the board
UART7_TX: U101.39 (PE8); also elsewhere on the board
UART8_RX: U101.97 (PE0); also elsewhere on the board
UART8_TX: U101.98 (PE1); also elsewhere on the board
USART1_CTS: U101.70 (PA11); also elsewhere on the board
USART1_RTS: U101.71 (PA12); also elsewhere on the board
USART1_RX: U101.69 (PA10); also elsewhere on the board
USART1_TX: U101.68 (PA9); also elsewhere on the board
USART2_CTS: U101.84 (PD3); also elsewhere on the board
USART2_RTS: U101.85 (PD4); also elsewhere on the board
USART2_RX: U101.87 (PD6); also elsewhere on the board
USART2_TX: U101.86 (PD5); also elsewhere on the board
USART3_CTS: U101.58 (PD11); also elsewhere on the board
USART3_RTS: U101.59 (PD12); also elsewhere on the board
USART3_RX: U101.56 (PD9); also elsewhere on the board
USART3_TX: U101.55 (PD8); also elsewhere on the board
USART6_RX: U101.64 (PC7); also elsewhere on the board
USART6_TX: U101.63 (PC6); also elsewhere on the board

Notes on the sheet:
STM32F4 IO Ports

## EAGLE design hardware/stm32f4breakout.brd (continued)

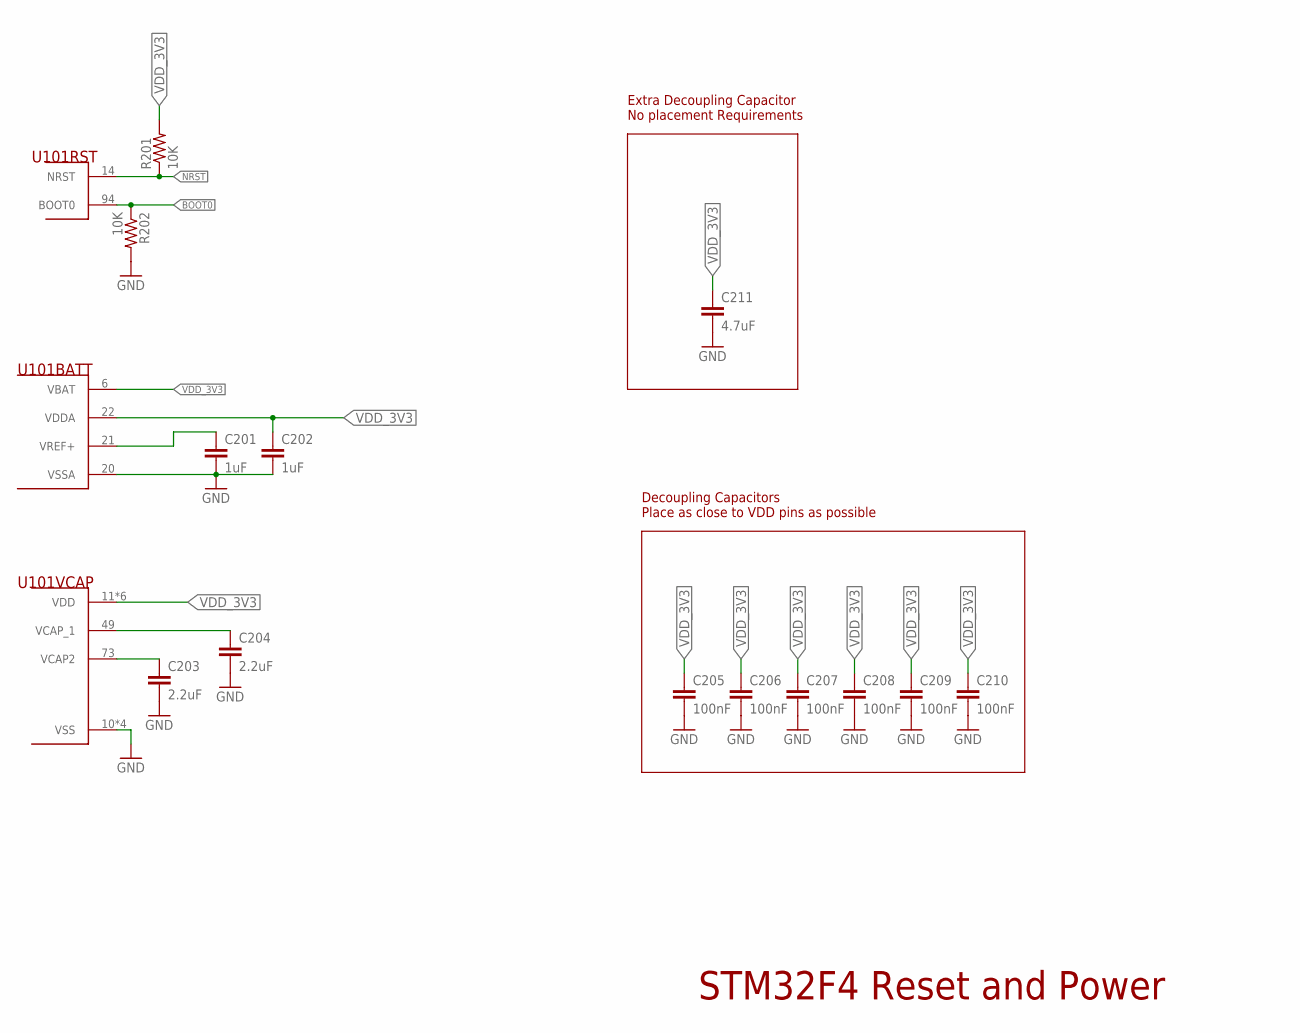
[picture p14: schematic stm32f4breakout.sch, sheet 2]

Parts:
C201, C202: 1uF; C0603
C203, C204: 2.2uF; C0603
C205, C206, C207, C208, C209, C210: 100nF; C0603
C211: 4.7uF; C0603
R201, R202: 10K; R0603
U101: STM32F427VGT6; LQFP-100

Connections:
BOOT0: R202.1, U101.94 (BOOT0); also elsewhere on the board
GND: C201.2, C202.2, C203.2, C204.2, C205.2, C206.2, C207.2, C208.2, C209.2, C210.2, C211.2, R202.2, U101.10 (VSS), U101.20 (VSSA), U101.27 (VSS), U101.74 (VSS), U101.99 (VSS); also elsewhere on the board
NRST: R201.1, U101.14 (NRST); also elsewhere on the board
VCAP2: C203.1, U101.73 (VCAP2)
VCAP_1: C204.1, U101.49 (VCAP_1)
VDD_3V3: C201.1, C202.1, C205.1, C206.1, C207.1, C208.1, C209.1, C210.1, C211.1, R201.2, U101.6 (VBAT), U101.11 (VDD), U101.19 (VDD), U101.21 (VREF+), U101.22 (VDDA), U101.28 (VDD), U101.50 (VDD), U101.75 (VDD), U101.100 (VDD); also elsewhere on the board

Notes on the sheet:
STM32F4 Reset and Power
Decoupling Capacitors Place as close to VDD pins as possible
Extra Decoupling Capacitor No placement Requirements

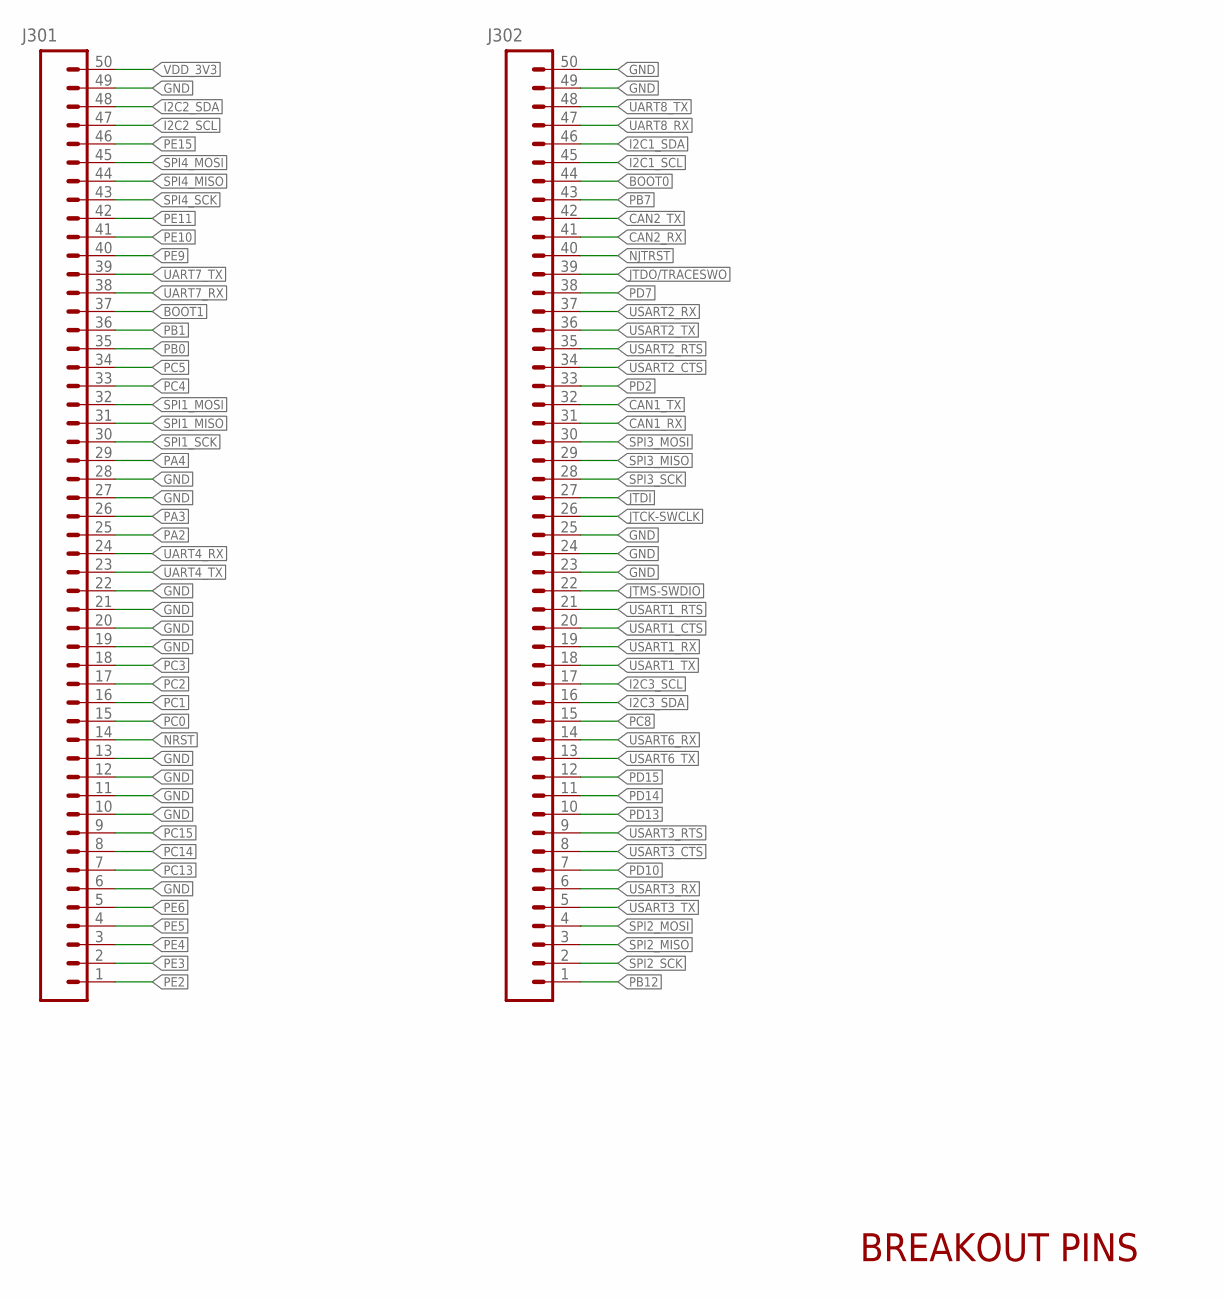
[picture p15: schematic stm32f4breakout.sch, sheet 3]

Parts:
J301, J302: PINHD-1X50; 1X50

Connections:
BOOT0: J302.44; also elsewhere on the board
BOOT1: J301.37; also elsewhere on the board
CAN1_RX: J302.31; also elsewhere on the board
CAN1_TX: J302.32; also elsewhere on the board
CAN2_RX: J302.41; also elsewhere on the board
CAN2_TX: J302.42; also elsewhere on the board
GND: J301.6, J301.10, J301.11, J301.12, J301.13, J301.19, J301.20, J301.21, J301.22, J301.27, J301.28, J301.49, J302.23, J302.24, J302.25, J302.49, J302.50; also elsewhere on the board
I2C1_SCL: J302.45; also elsewhere on the board
I2C1_SDA: J302.46; also elsewhere on the board
I2C2_SCL: J301.47; also elsewhere on the board
I2C2_SDA: J301.48; also elsewhere on the board
I2C3_SCL: J302.17; also elsewhere on the board
I2C3_SDA: J302.16; also elsewhere on the board
JTCK-SWCLK: J302.26; also elsewhere on the board
JTDI: J302.27; also elsewhere on the board
JTDO/TRACESWO: J302.39; also elsewhere on the board
JTMS-SWDIO: J302.22; also elsewhere on the board
NJTRST: J302.40; also elsewhere on the board
NRST: J301.14; also elsewhere on the board
PA2: J301.25; also elsewhere on the board
PA3: J301.26; also elsewhere on the board
PA4: J301.29; also elsewhere on the board
PB0: J301.35; also elsewhere on the board
PB1: J301.36; also elsewhere on the board
PB7: J302.43; also elsewhere on the board
PB12: J302.1; also elsewhere on the board
PC0: J301.15; also elsewhere on the board
PC1: J301.16; also elsewhere on the board
PC2: J301.17; also elsewhere on the board
PC3: J301.18; also elsewhere on the board
PC4: J301.33; also elsewhere on the board
PC5: J301.34; also elsewhere on the board
PC8: J302.15; also elsewhere on the board
PC13: J301.7; also elsewhere on the board
PC14: J301.8; also elsewhere on the board
PC15: J301.9; also elsewhere on the board
PD2: J302.33; also elsewhere on the board
PD7: J302.38; also elsewhere on the board
PD10: J302.7; also elsewhere on the board
PD13: J302.10; also elsewhere on the board
PD14: J302.11; also elsewhere on the board
PD15: J302.12; also elsewhere on the board
PE2: J301.1; also elsewhere on the board
PE3: J301.2; also elsewhere on the board
PE4: J301.3; also elsewhere on the board
PE5: J301.4; also elsewhere on the board
PE6: J301.5; also elsewhere on the board
PE9: J301.40; also elsewhere on the board
PE10: J301.41; also elsewhere on the board
PE11: J301.42; also elsewhere on the board
PE15: J301.46; also elsewhere on the board
SPI1_MISO: J301.31; also elsewhere on the board
SPI1_MOSI: J301.32; also elsewhere on the board
SPI1_SCK: J301.30; also elsewhere on the board
SPI2_MISO: J302.3; also elsewhere on the board
SPI2_MOSI: J302.4; also elsewhere on the board
SPI2_SCK: J302.2; also elsewhere on the board
SPI3_MISO: J302.29; also elsewhere on the board
SPI3_MOSI: J302.30; also elsewhere on the board
SPI3_SCK: J302.28; also elsewhere on the board
SPI4_MISO: J301.44; also elsewhere on the board
SPI4_MOSI: J301.45; also elsewhere on the board
SPI4_SCK: J301.43; also elsewhere on the board
UART4_RX: J301.24; also elsewhere on the board
UART4_TX: J301.23; also elsewhere on the board
UART7_RX: J301.38; also elsewhere on the board
UART7_TX: J301.39; also elsewhere on the board
UART8_RX: J302.47; also elsewhere on the board
UART8_TX: J302.48; also elsewhere on the board
USART1_CTS: J302.20; also elsewhere on the board
USART1_RTS: J302.21; also elsewhere on the board
USART1_RX: J302.19; also elsewhere on the board
USART1_TX: J302.18; also elsewhere on the board
USART2_CTS: J302.34; also elsewhere on the board
USART2_RTS: J302.35; also elsewhere on the board
USART2_RX: J302.37; also elsewhere on the board
USART2_TX: J302.36; also elsewhere on the board
USART3_CTS: J302.8; also elsewhere on the board
USART3_RTS: J302.9; also elsewhere on the board
USART3_RX: J302.6; also elsewhere on the board
USART3_TX: J302.5; also elsewhere on the board
USART6_RX: J302.14; also elsewhere on the board
USART6_TX: J302.13; also elsewhere on the board
VDD_3V3: J301.50; also elsewhere on the board

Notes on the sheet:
BREAKOUT PINS

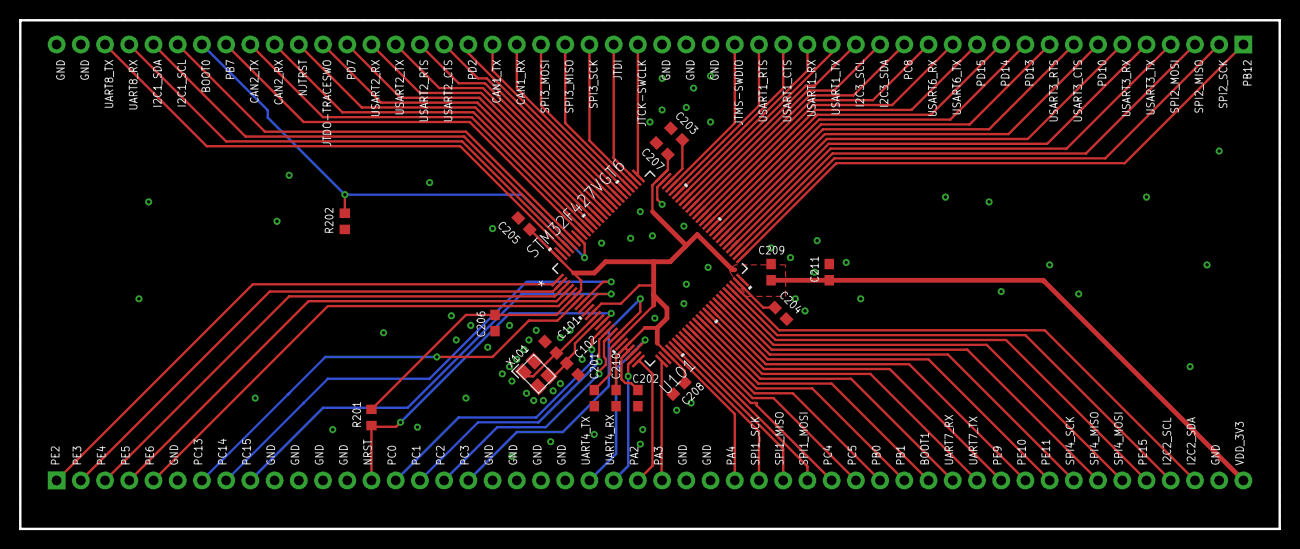
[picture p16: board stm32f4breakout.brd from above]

Board: 2 copper layers, 132.1 x 53.3 mm, 19 parts (0 on the bottom side), 88 nets.

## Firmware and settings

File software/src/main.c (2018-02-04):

#include "stm32f4xx.h"
#include "stm32f4xx_rcc.h"
#include "stm32f4xx_gpio.h"
#include "stm32f4xx_tim.h"

#include "uart.h"
#include "i2c.h"
#include "tim.h"
#include "util.h"
#include "bno055.h"
#include "pid.h"

#define ANGLE_KILL 0


#define MOTOR1 4
#define MOTOR2 1
#define MOTOR3 2
#define MOTOR4 3
#define N MOTOR2
#define W MOTOR3
#define S MOTOR4
#define E MOTOR1

#define N_OFFSET (-5.0)
#define W_OFFSET (-4.0)
#define S_OFFSET (0.0)
#define E_OFFSET (0.0)

#define CALIBRATE 0

int main() {
  SystemInit();

  tim_init();
  pwm_init();

  set_pwm(N, 0.0);
  set_pwm(W, 0.0);
  set_pwm(S, 0.0);
  set_pwm(E, 0.0);

  usart1_init(B115200);

  i2c_init();

  if(bno055_init() != 0) {
    usart1_puts("Failed to initialize BNO055\n");
    while(1);
  }
  usart1_puts("bno055 initialized\n");

#if CALIBRATE == 1
  bno055_do_calibration();
  while(1);
#else
  bno055_load_calibration();
  usart1_puts("BNO055 calibration loaded\n");
#endif

  pid_t pid_r, pid_p, pid_y;
  pid_init(&pid_r, 0.12, 0.05, 0.0, -20.0, 20.0);
  pid_init(&pid_p, 0.12, 0.05, 0.0, -20.0, 20.0);
  pid_init(&pid_y, 0.0, 0.0, 0.0, -10.0, 10.0);
  pid_setpoint(&pid_r, 0.0);
  pid_setpoint(&pid_p, 0.0);
  pid_setpoint(&pid_y, 0.0);
  float throttle = 0.0;
  float max_throttle = 35.0;

  float step = (max_throttle-throttle)/100;

  float rpy[3];
  float gyro[3];
  periodic_init(100);

#if 0
  usart1_puts("entering sleep\n");
  for(int i=0; i < 5000; i++) {
    sleep_ms(1);
  }
  usart1_puts("out of sleep\n");
#endif

  // Bring throttle up to 50%
  for(int i=0; i < 200; i++) {
    periodic_sleep();
    bno055_get_rpy(rpy);
    bno055_get_gyro(gyro);

    float roll = pid_update(&pid_r, rpy[0], gyro[0]);
    float pitch = pid_update(&pid_p, rpy[1], gyro[1]);
    float yaw = pid_update(&pid_y, rpy[2], gyro[2]);

    set_pwm(N, throttle + pitch - yaw);
    set_pwm(S, throttle - pitch - yaw);
    set_pwm(W, throttle + roll + yaw);
    set_pwm(E, throttle - roll + yaw);
    throttle += step;
  }

  // Hold throttle at 50%
  for(int i=0; i < 200; i++) {
    periodic_sleep();
    bno055_get_rpy(rpy);
    bno055_get_gyro(gyro);

    for(int i=0; i < sizeof(rpy); i++) {
      usart1_putc(((char *)rpy)[i]);
    }
    usart1_putc((char)0xff);

#if ANGLE_KILL
    if(rpy[0] > 30.0 || rpy[0] < -30.0
        || rpy[1] > 30.0 || rpy[1] < -30.0) {
      set_pwm(N, 0);
      set_pwm(S, 0);
      set_pwm(W, 0);
      set_pwm(E, 0);
      while(1);
    }
#endif // ANGLE_KILL
    float roll = pid_update(&pid_r, rpy[0], gyro[0]);
    float pitch = pid_update(&pid_p, rpy[1], gyro[1]);
    float yaw = pid_update(&pid_y, rpy[2], gyro[2]);

    set_pwm(N, throttle - pitch - yaw + N_OFFSET);
    set_pwm(S, throttle + pitch - yaw + S_OFFSET);
    set_pwm(W, throttle + roll + yaw + W_OFFSET);
    set_pwm(E, throttle - roll + yaw + E_OFFSET);
  }
  // Bring throttle down to 0% 
  // for(int i=0; i < 300; i++) {
  while(1) {
    periodic_sleep();
    bno055_get_rpy(rpy);
    bno055_get_gyro(gyro);
    for(int i=0; i < sizeof(rpy); i++) {
      usart1_putc(((char *)rpy)[i]);
    }
    usart1_putc((char)0xff);
    /* usart1_puts("Orientation: "); */
    /* print_float(rpy[0]); */
    /* usart1_putc(' '); */
    /* print_float(rpy[1]); */
    /* usart1_putc(' '); */
    /* print_float(rpy[2]); */
    /* usart1_putc('\n'); */

    /* for(int i=0; i < sizeof(rpy); i++) { */
    /*   usart1_putc(((char *)rpy)[i]); */
    /* } */
    /* usart1_putc((char)0xff); */

#if ANGLE_KILL
    if(rpy[0] > 30.0 || rpy[0] < -30.0
        || rpy[1] > 30.0 || rpy[1] < -30.0) {
      set_pwm(N, 0);
      set_pwm(S, 0);
      set_pwm(W, 0);
      set_pwm(E, 0);
      while(1);
    }
#endif // ANGLE_KILL

    float roll = pid_update(&pid_r, rpy[0], gyro[0]);
    float pitch = pid_update(&pid_p, rpy[1], gyro[1]);
    float yaw = pid_update(&pid_y, rpy[2], gyro[2]);

    set_pwm(N, throttle - pitch - yaw + N_OFFSET);
    set_pwm(S, throttle + pitch - yaw + S_OFFSET);
    set_pwm(W, throttle + roll + yaw + W_OFFSET);
    set_pwm(E, throttle - roll + yaw + E_OFFSET);
  }

  step = max_throttle / 300;
  for(int i=0; i < 300; i++) {
    periodic_sleep();
    bno055_get_rpy(rpy);
    bno055_get_gyro(gyro);

    if(rpy[0] > 30.0 || rpy[0] < -30.0
        || rpy[1] > 30.0 || rpy[1] < -30.0) {
      set_pwm(N, 0);
      set_pwm(S, 0);
      set_pwm(W, 0);
      set_pwm(E, 0);
      while(1);
    }

    float roll = pid_update(&pid_r, rpy[0], gyro[0]);
    float pitch = pid_update(&pid_p, rpy[1], gyro[1]);
    float yaw = pid_update(&pid_y, rpy[2], gyro[2]);

    set_pwm(N, throttle - pitch - yaw + N_OFFSET);
    set_pwm(S, throttle + pitch - yaw + S_OFFSET);
    set_pwm(W, throttle + roll + yaw + W_OFFSET);
    set_pwm(E, throttle - roll + yaw + E_OFFSET);

    throttle -= step;
  }

  set_pwm(N, 0);
  set_pwm(S, 0);
  set_pwm(W, 0);
  set_pwm(E, 0);
  while(1);

  return 0;
}

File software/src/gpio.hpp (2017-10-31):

#ifndef GPIO_H
#define GPIO_H
#include "stm32f4xx.h"


class GPIO {
  public:
    enum Pin {
      PIN0  = 0,
      PIN1  = 1,
      PIN2  = 2,
      PIN3  = 3,
      PIN4  = 4,
      PIN5  = 5,
      PIN6  = 6,
      PIN7  = 7,
      PIN8  = 8,
      PIN9  = 9,
      PIN10 = 10,
      PIN11 = 11,
      PIN12 = 12,
      PIN13 = 13,
      PIN14 = 14,
      PIN15 = 15,
    };

    enum Mode {
      INPUT=0x0,
      OUTPUT=0x1,
      ALTERNATE=0x2,
      ANALOG=0x3,
    };

    enum OType {
      PUSHPULL=0x0,
      OPENDRAIN=0x1,
    };

    enum OSpeed {
      LOW=0x0,
      MEDIUM=0x1,
      HIGH=0x2,
      VERYHIGH=0x3,
    };

    enum IPull {
      NONE=0x0,
      UP=0x1,
      DOWN=0x2,
    };

    GPIO(GPIO_TypeDef *bank);

    bool SetMode(Pin pin, Mode mode);
    bool SetOType(Pin pin, OType type);
    bool SetOSpeed(Pin pin, OSpeed speed);
    bool SetIPull(Pin pin, IPull pull);

    void Set(Pin pin);
    void Reset(Pin pin);
    bool Get(Pin pin);

  private:
    GPIO_TypeDef *bank_;
};
#endif // GPIO_H

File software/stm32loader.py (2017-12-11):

#!/usr/bin/env python2

# -*- coding: utf-8 -*-
# vim: sw=4:ts=4:si:et:enc=utf-8

# Author: Ivan A-R <ivan@tuxotronic.org>
# Project page: http://tuxotronic.org/wiki/projects/stm32loader
#
# This file is part of stm32loader.
#
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
import sys, getopt
import serial
import time

try:
    from progressbar import *
    usepbar = 1
except:
    usepbar = 0

# Verbose level
QUIET = 20

# these come from AN2606
chip_ids = {
    0x412: "STM32 Low-density",
    0x410: "STM32 Medium-density",
    0x414: "STM32 High-density",
    0x420: "STM32 Medium-density value line",
    0x428: "STM32 High-density value line",
    0x430: "STM32 XL-density",
    0x416: "STM32 Medium-density ultralow power line",
    0x411: "STM32F2xx",
    0x413: "STM32F4xx",
    0x419: "STM32F427",
}

def mdebug(level, message):
    if(QUIET >= level):
        print >> sys.stderr , message


class CmdException(Exception):
    pass

class CommandInterface:
    extended_erase = 0

    def open(self, aport='/dev/ttyUSB0', abaudrate=115200) :
        # self.sp = serial.Serial(
        #     port=aport,
        #     baudrate=abaudrate,
        #     bytesize=8,
        #     parity=serial.PARITY_EVEN,
        #     stopbits=1,
        #     xonxoff=0,
        #     rtscts=0,
        #     timeout=5,
        # )
        self.sp = serial.Serial()
        self.sp.port = aport
        self.sp.baudrate = abaudrate     # baudrate
        self.sp.bytesize = 8             # number of databits
        self.sp.parity = serial.PARITY_EVEN
        self.sp.stopbits = 1
        self.sp.xonxoff = 0              # don't enable software flow control
        self.sp.rtscts = 0               # don't enable RTS/CTS flow control
        self.sp.dsrdtr = False
        self.sp.timeout = 5              # set a timeout value, None for waiting forever
        self.sp.rts = False
        self.sp.dtr = False
        self.sp.open()


    def _wait_for_ask(self, info = ""):
        # wait for ask
        try:
            ask = ord(self.sp.read())
        except:
            raise CmdException("Can't read port or timeout")
        else:
            if ask == 0x79:
                # ACK
                return 1
            else:
                if ask == 0x1F:
                    # NACK
                    raise CmdException("NACK "+info)
                else:
                    # Unknown responce
                    raise CmdException("Unknown response. "+info+": "+hex(ask))


    def reset(self):
        self.sp.setRTS(1)
        time.sleep(0.1)
        self.sp.setRTS(0)
        time.sleep(0.5)

    def initChip(self):
        # Set boot
        self.sp.setDTR(0)
        self.reset()

        self.sp.write("\x7F")       # Syncro
        self.sp.setDTR(1)
        return self._wait_for_ask("Syncro")

    def releaseChip(self):
        # self.sp.setDTR(1)
        # time.sleep(0.1)
        self.reset()

        # self.sp.setDTR(0)

    def cmdGeneric(self, cmd):
        self.sp.write(chr(cmd))
        self.sp.write(chr(cmd ^ 0xFF)) # Control byte
        return self._wait_for_ask(hex(cmd))

    def cmdGet(self):
        if self.cmdGeneric(0x00):
            mdebug(10, "*** Get command");
            len = ord(self.sp.read())
            version = ord(self.sp.read())
            mdebug(10, "    Bootloader version: "+hex(version))
            dat = map(lambda c: hex(ord(c)), self.sp.read(len))
            if '0x44' in dat:
                self.extended_erase = 1
            mdebug(10, "    Available commands: "+", ".join(dat))
            self._wait_for_ask("0x00 end")
            return version
        else:
            raise CmdException("Get (0x00) failed")

    def cmdGetVersion(self):
        if self.cmdGeneric(0x01):
            mdebug(10, "*** GetVersion command")
            version = ord(self.sp.read())
            self.sp.read(2)
            self._wait_for_ask("0x01 end")
            mdebug(10, "    Bootloader version: "+hex(version))
            return version
        else:
            raise CmdException("GetVersion (0x01) failed")

    def cmdGetID(self):
        if self.cmdGeneric(0x02):
            mdebug(10, "*** GetID command")
            len = ord(self.sp.read())
            id = self.sp.read(len+1)
            self._wait_for_ask("0x02 end")
            return reduce(lambda x, y: x*0x100+y, map(ord, id))
        else:
            raise CmdException("GetID (0x02) failed")


    def _encode_addr(self, addr):
        byte3 = (addr >> 0) & 0xFF
        byte2 = (addr >> 8) & 0xFF
        byte1 = (addr >> 16) & 0xFF
        byte0 = (addr >> 24) & 0xFF
        crc = byte0 ^ byte1 ^ byte2 ^ byte3
        return (chr(byte0) + chr(byte1) + chr(byte2) + chr(byte3) + chr(crc))


    def cmdReadMemory(self, addr, lng):
        assert(lng <= 256)
        if self.cmdGeneric(0x11):
            mdebug(10, "*** ReadMemory command")
            self.sp.write(self._encode_addr(addr))
            self._wait_for_ask("0x11 address failed")
            N = (lng - 1) & 0xFF
            crc = N ^ 0xFF
            self.sp.write(chr(N) + chr(crc))
            self._wait_for_ask("0x11 length failed")
            return map(lambda c: ord(c), self.sp.read(lng))
        else:
            raise CmdException("ReadMemory (0x11) failed")


    def cmdGo(self, addr):
        if self.cmdGeneric(0x21):
            mdebug(10, "*** Go command")
            self.sp.write(self._encode_addr(addr))
            self._wait_for_ask("0x21 go failed")
        else:
            raise CmdException("Go (0x21) failed")


    def cmdWriteMemory(self, addr, data):
        assert(len(data) <= 256)
        if self.cmdGeneric(0x31):
            mdebug(10, "*** Write memory command")
            self.sp.write(self._encode_addr(addr))
            self._wait_for_ask("0x31 address failed")
            #map(lambda c: hex(ord(c)), data)
            lng = (len(data)-1) & 0xFF
            mdebug(10, "    %s bytes to write" % [lng+1]);
            self.sp.write(chr(lng)) # len really
            crc = 0xFF
            for c in data:
                crc = crc ^ c
                self.sp.write(chr(c))
            self.sp.write(chr(crc))
            self._wait_for_ask("0x31 programming failed")
            mdebug(10, "    Write memory done")
        else:
            raise CmdException("Write memory (0x31) failed")


    def cmdEraseMemory(self, sectors = None):
        if self.extended_erase:
            return cmd.cmdExtendedEraseMemory()
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

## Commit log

2017-09-15 Continue work on schematic
    [quad.brd, quad.sch]
2017-09-18 Create breakout board for STM32F4
    [stm32f4breakout.brd, stm32f4breakout.sch]
2017-09-18 Add 4.7uF decoupling cap
    [stm32f4breakout.brd, stm32f4breakout.sch]
2017-09-18 Add breakout schematic pdf
2017-09-19 Fix final airwires on breakout, add DRC file
    [stm32f4breakout.brd, stm32f4breakout.sch]
2017-09-22 Add USB-UART, BNO055
    [quad.brd, quad.sch]
2017-09-25 Wire BNO055, Added XBEE
    [quad.brd, quad.sch]
2017-09-26 Add power connectors, finish BNO055
    [quad.brd, quad.sch]
2017-09-29 First draft schematic done
    [quad.brd, quad.sch]
2017-09-29 Fixes and start layout
    [quad.brd, quad.sch]
2017-10-02 Add board outline and make some placements
    [Board_Outline.DXF, import-dxf.cfg, quad.brd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]
2017-10-03 Passing DRC on the layout
    [quad.brd, quad.sch]
2017-10-13 Redo board power layout
    [quad.brd, quad.sch]
2017-10-21 Minor changes
    [quad.brd, quad.sch]
2017-10-23 Every interrupt vector MUST have LSB set to 0
    This is required by the ARM cortex architecture to indicate that the
    code is thumb code
2017-10-24 Set PLL frequency to match board
2017-10-31 Working uart
2017-11-03 Set HSE oscillator value
    [i2c.c, main.c, uart.c]
2017-11-06 Working I2C
2017-11-10 Fix up I2C bugs, initial working bno055
    [bno055.c, i2c.c, main.c]
2017-11-13 Not working, but progress
    [bno055.c, graph_imu.py, main.c]
2017-11-15 Working PWM Timer
    Added standard peripheral drivers for timer support, created function for PWM control on TIM3
2017-11-27 Add periodic timer commands, sleep commands, reformat
2017-11-27 Try to sample the bno again
2017-11-28 Make BNO055 use external crystal.
    As of this commit, the bno055 outputs very good fused data.
2017-11-28 Start pid
2017-12-01 Add calibration for IMU
2017-12-05 Replace loader script, can flash board but no responses
    [stm32loader.py]
2017-12-10 Changed PWM frequency and lower/upper bounds
    Changed PWM frequency from 500Hz to 100Hz and set the lower bound of the motor control to 1ms and the upper bound to 2ms
2017-12-11 Set right motors

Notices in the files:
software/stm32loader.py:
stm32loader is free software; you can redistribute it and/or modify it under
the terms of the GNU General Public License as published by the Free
